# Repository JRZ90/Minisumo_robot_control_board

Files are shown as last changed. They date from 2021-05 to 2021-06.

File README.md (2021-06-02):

## Minisumo robot control board
Custom control board for mini sumo robots with an ATmega 328 as the main controller, a TB6612 for motor control, connections for up to 5 analog or digital opponent sensors, 3 "dohyo" line sensors, 2 user buttons and a dip -switch for quick strategy configuration. This board can work with a 2 or 3 cell lipo battery.

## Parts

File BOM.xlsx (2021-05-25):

Comment | Designator | Footprint | LCSC Part #
lm324 | U3, U4 | SOIC-14_150mil | C71035
atmega328 | U2 | TQFP-32_7x7x08P | C14877
TB6612 | U5 | SSOP-24 | C141517
Dipswitch | SW4 | Through Hole | C52648
ASM1117-5.0 | U1 | SOT-223 | C6187
TC33X-2-103E | TM1, TM2, TM3, TM4, TM5, TM6, TM7, TM8 | SMD | C719176
TS-1187A-C-E-B | SW2, SW3, SW5 | SMD | C318887
R10K | R1, R2, R6, R7, R8, R9, R10, R11, R12, R13, R14, R15, R16 | 0603 | C98220
R330R | R3 | 0603 | C23138
R1K | R4, R5 | 0603 | C21190
C100nF | C3, C4, C5, C6, C7, C11, C12, C13, C14 | 0603 | C14663
C4,7uF | C1, C2 | 0603 | C1705
C22pF | C9, C10 | 0603 | C1653
C1000uF/16V | C8 | SMD,10x10.2mm | C249474
NX3225GA-16MHZ | X1 | SMD-3225_4P | C156247
K3-1260D-L1 | SW1 | Through Hole | C92657
0805 LED | D1 | 0805 | C72035

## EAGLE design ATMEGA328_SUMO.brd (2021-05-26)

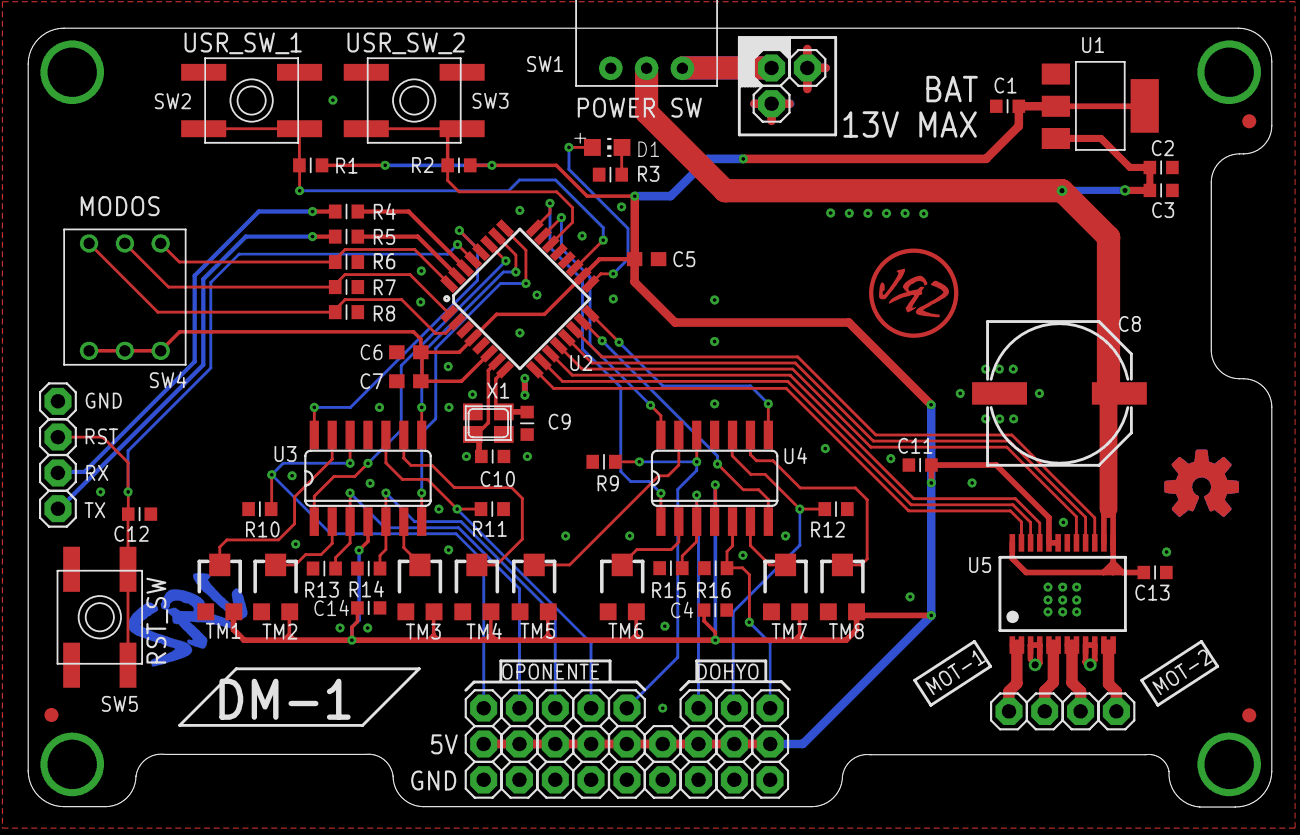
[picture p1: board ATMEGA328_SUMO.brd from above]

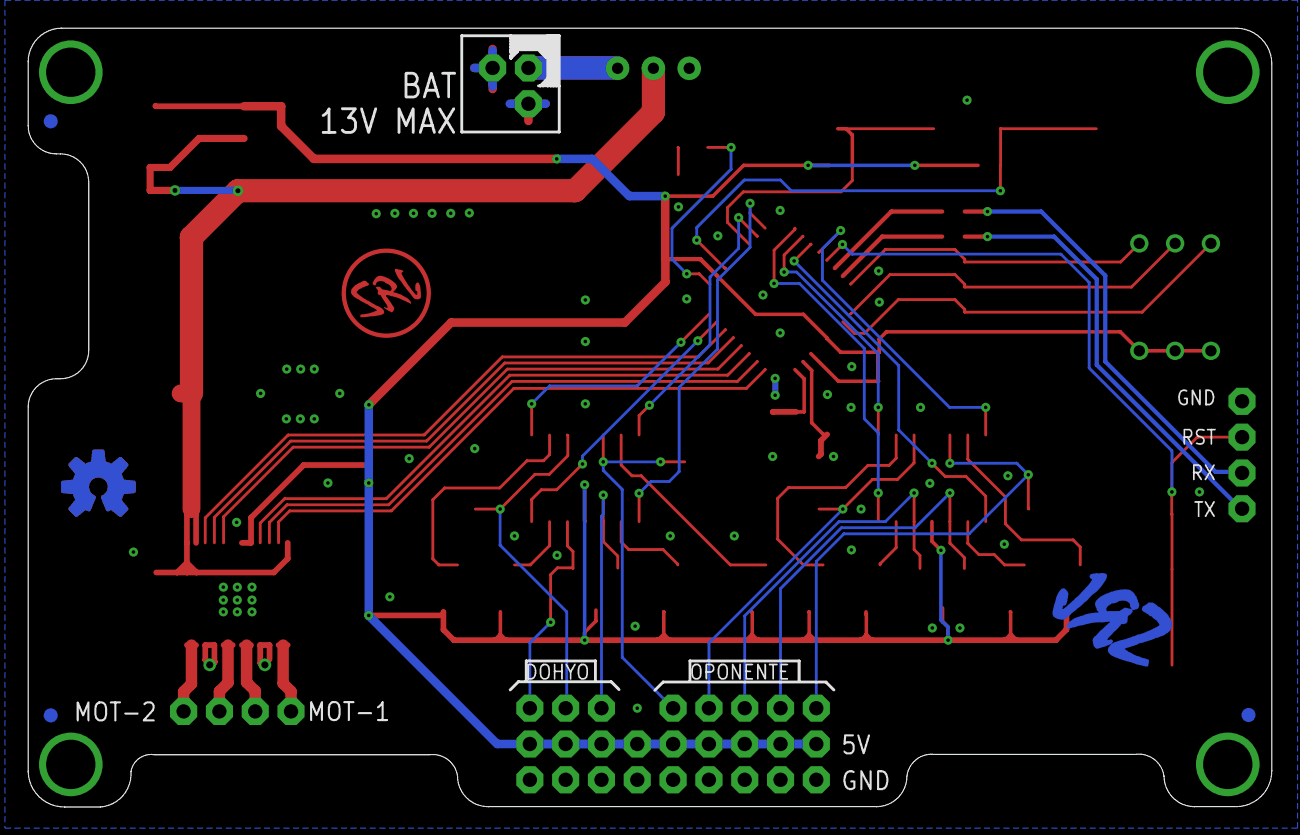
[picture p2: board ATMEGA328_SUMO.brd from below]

Board: 2 copper layers, 88.2 x 55.2 mm, 96 parts (4 on the bottom side), 52 nets.

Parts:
C1, C2: 4.7uF; CAPC1608X92N
C3, C4, C11, C12, C13, C14: 100nF; CAPC1608X92N
C5, C6, C7: 100nF; C0603
C8: 2200uF/16V; PANASONIC_G
C9, C10: 22pF; CAPC1608X92N
D1: CHIP-LED0805
JP1, JP2, JP3, JP4, JP5, JP6, JP7, JP8, JP9, JP10, JP11, JP12, JP13, JP14, JP15, JP16, JP17, JP18, JP19, JP20, JP21, JP22, JP23, JP24, JP25, JP26, JP27, JP28, JP29, JP30, JP31, JP32, JP33: 1X01
MOT-1A1, MOT-1A2, MOT-1B1, MOT-1B2: 1X01
R1: R4; RESC1608X55N
R2, R6, R7, R8, R9, R10, R11, R12, R13, R14, R15, R16: 10K; RESC1608X55N
R3: 330R; RESC1608X55N
R4, R5: 1K; RESC1608X55N
SW1: LCSC-C92657; 450302014072
SW2: LCSC_C318887; EVQ-Q2
SW3, SW5: SPST_TACT-EVQQ2__C318887; EVQ-Q2
SW4: LCSC-C52648; 418117170903
TM1, TM2, TM3, TM4, TM5, TM6, TM7, TM8: 10K; TC33X
U1: AMS1117-5.0__C6187; SOT-223
U2: ATMEGA328P_TQFP; TQFP32-08
U3, U4: LM324D; SO14
U5: TB6612FNG; SSOP24
U$1, U$3, U$4, U$100, U$101, U$102: FIDUCIAL; FIDUCIAL_1MM
U$2: LOGO_B
U$6, U$7: OSHWLOGO_TOP_0.2
X1: 16MHz; NX3225

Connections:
5V: C1.2, C4.1, C5.1, C6.1, C7.1, C11.1, C14.1, JP16.1, JP17.1, JP18.1, JP19.1, JP20.1, JP21.1, JP22.1, JP23.1, JP24.1, R1.2, R2.2, SW4.1, SW4.2, SW4.3, TM1.3, TM2.3, TM3.3, TM4.3, TM5.3, TM6.3, TM7.3, TM8.3, U1.2, U1.4, U2.4, U2.6, U2.18, U3.4, U4.4, U5.19, U5.20
BAT+: C2.2, C3.2, C8.+, C13.2, SW1.1, U1.3, U5.13, U5.14, U5.24
DS1: R6.1, SW4.4, U2.32
DS2: R7.1, SW4.5, U2.1
DS3: R8.1, SW4.6, U2.2
GND: C1.1, C2.1, C3.1, C4.2, C5.2, C6.2, C7.2, C8.-, C9.2, C10.2, C11.2, C12.2, C13.1, C14.2, JP2.1, JP3.1, JP4.1, JP25.1, JP26.1, JP27.1, JP28.1, JP29.1, JP30.1, JP31.1, JP32.1, JP33.1, R3.1, R6.2, R7.2, R8.2, R9.2, R10.1, R11.1, R12.1, R13.1, R14.1, R15.1, R16.1, SW2.A, SW2.A', SW3.A, SW3.A', SW5.B, SW5.B', TM1.1, TM2.1, TM3.1, TM4.1, TM5.1, TM6.1, TM7.1, TM8.1, U1.1, U2.3, U2.5, U2.21, U3.11, U4.11, U5.3, U5.4, U5.9, U5.10, U5.18, X1.2, X1.4
IN1_M1: U2.11, U5.21
IN1_M2: U2.12, U5.17
IN2_M1: U2.10, U5.22
IN2_M2: U2.13, U5.16
LED_PIN: D1.A, U2.17
unnamed: D1.C, R3.2
unnamed: JP10.1, R14.2, U3.5
unnamed: JP11.1, R11.2, U3.10
unnamed: TM2.2, U3.2
unnamed: TM3.2, U3.6
unnamed: TM4.2, U3.9
unnamed: MOT-1B2.1, U5.5, U5.6
unnamed: TM1.2, U3.13
unnamed: TM5.2, U4.13
unnamed: JP12.1, R9.1, U4.12
unnamed: TM6.2, U4.2
unnamed: JP8.1, R10.2, U3.12
unnamed: JP13.1, R15.2, U4.3
unnamed: JP9.1, R13.2, U3.3
unnamed: MOT-1B1.1, U5.1, U5.2
unnamed: C9.1, U2.8, X1.1
unnamed: C10.1, U2.7, X1.3
unnamed: MOT-1A2.1, U5.11, U5.12
unnamed: MOT-1A1.1, U5.7, U5.8
unnamed: TM7.2, U4.6
unnamed: JP15.1, R16.2, U4.5
unnamed: JP1.1, SW1.3
unnamed: TM8.2, U4.9
unnamed: JP14.1, R12.2, U4.10
PB3: U2.15, U4.7
PB4: U2.16, U4.8
PC0: U2.23, U4.14
PC1: U2.24, U4.1
PC2: U2.25, U3.7
PC3: U2.26, U3.8
PC4: U2.27, U3.1
PC5: U2.28, U3.14
PWM_M1: U2.9, U5.23
PWM_M2: U2.14, U5.15
RST: C12.1, JP5.1, SW5.A, SW5.A', U2.29
RX: JP6.1, R4.1
RX.: R4.2, U2.30
TX: JP7.1, R5.1
TX.: R5.2, U2.31
USR_SW1: R2.1, SW3.B, SW3.B', U2.22
USR_SW2: R1.1, SW2.B, SW2.B', U2.19

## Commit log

2021-05-25 primer commit, todo funciona pero falta terminar algunas cosas
    [ATMEGA328_SUMO.brd, ATMEGA328_SUMO.sch]
2021-05-25 Segundo commit con todo listo para compartir
    [BOM.xlsx, PNP.xlsx]
2021-05-26 correccion de algunos errores menores en DRC
    [ATMEGA328_SUMO.brd]
2021-05-26 correccion de algunos herrores menores en ERC
    [ATMEGA328_SUMO.sch]

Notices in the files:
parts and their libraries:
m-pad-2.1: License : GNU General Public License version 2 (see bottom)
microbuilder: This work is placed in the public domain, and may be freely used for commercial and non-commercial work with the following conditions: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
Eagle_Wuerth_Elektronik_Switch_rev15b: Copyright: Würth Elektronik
